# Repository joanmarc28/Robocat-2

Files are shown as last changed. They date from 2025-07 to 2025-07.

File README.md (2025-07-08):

<h1 align="center">
  <br>
    RoboCat Logo
  <br>
    RoboCat
  <br>
</h1>

<h4 align="center">A quadruped robot developed by third-year Computer Science students at the Universitat Autònoma de Barcelona.</h4>

<p align="center">
  <!----------------------- UAB | Robótica ----------------------->
  
  <!--------------------------- Status --------------------------->
  
  <!---------------------------  Raspi --------------------------->
  <a href="https://www.raspberrypi.com/">
  </a>
  <!--------------------------- THX U ---------------------------->
  
  
</p>

 <!---Modificar per els nostres casos--->
<p align="center">
  <a href="#What-is-RoboCat">What is RoboCat?</a> •
  <a href="#How-To-Use">How to use</a> •
  <a href="#Components">Components</a> •
  <a href="#Software">Software</a> •
  <a href="#Tech-Stack">Tech Stack</a> •
  <a href="#License">License</a> •
  <a href="#Contribution">Contribution</a> •
  <a href="#References">References</a> •
  <a href="#Credits">Credits</a> •
  <a href="#Gallery">Gallery</a>
</p>



# What is RoboCat?

RoboCat is an autonomous quadruped robot designed to patrol public streets and monitor parking zones regulated by payment. Its structure and external appearance are inspired by a cat's shape, making it functional but also friendly and approachable for pedestrians.
Equipped with sensors, cameras and onboard computing, RoboCat can detect whether a parked vehicle has an active parking permit, combining robotics, computer vision and real-time data processing to offer a smart, mobile solution for urban mobility enforcement.

The project's main goals are to:
  - Automate parking control in regulated areas
  - Reduce the need for manual inspection
  - Integrate urban robotics with a friendly and non-threatening design
  - Demonstrate the application of robotics in real-world city environments

<p align="center">
  <a href="https://www.youtube.com/watch?v=SMAzvaqW83E" target="_blank">
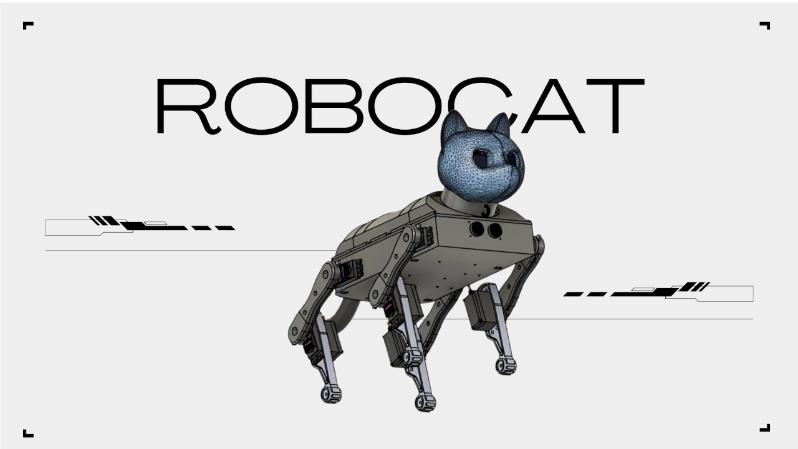
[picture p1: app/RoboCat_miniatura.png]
Miniatura del vídeo
    
  </a>
</p>
<p>
  <a href="https://www.youtube.com/watch?v=SMAzvaqW83E" target="_blank">
    View Video on YouTube
  </a>
</p>
  
# How to use

To set up and run RoboCat on your system, follow these simple steps:
### Step 1: Download the repository
Open your terminal and run the following command:
```bash
git clone https://github.com/joanmarc28/Robocat.git
cd Robocat
```
### Step 2: Install dependencies
Make sure you have Python installed. You can install the required environment simply by running the file setup_robocat.sh:
```bash
bash setup_robocat.sh
```
You can run this command even if the robot is powered off. The setup process only installs software on your computer.

#### How do I install Python?
If you don't have Python installed, download it from the [official website](https://www.python.org/downloads/)
You can check your Python version by running:
```bash
python --version
```
### Step 3: Activate the environment
Once the installation is complete, activate the virtual environment and run the main program by running the following command:
```bash
bash start_robocat.sh
```
Now you can just enjoy!

# Components

## Hardware 

The RoboCat prototype integrates various electronic modules connected to the Raspberry Pi 4, which is the central processing unit.

### Required components
| Component | Model | Units |
|---|---|---|
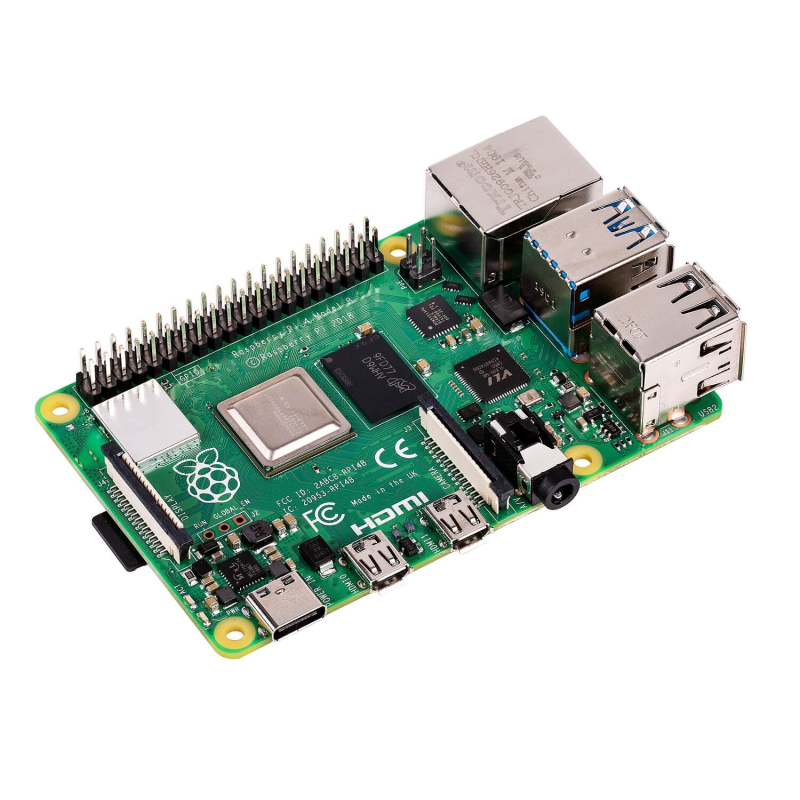
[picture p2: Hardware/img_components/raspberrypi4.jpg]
|  | [Raspberry Pi 4 Model B](https://tienda.bricogeek.com/placas-raspberry-pi/1330-raspberry-pi-4-model-b-4-gb.html) | 1 |
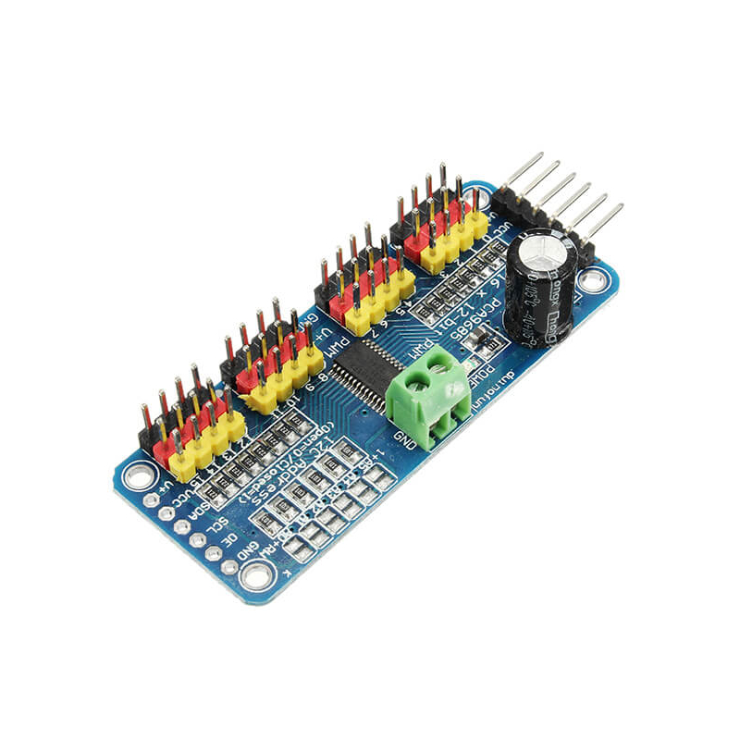
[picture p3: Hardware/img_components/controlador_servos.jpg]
|  | [PCA9685 (16 channel PWM controller)](https://tienda.bricogeek.com/controladores-motores/1764-controlador-pwm-16-canales-i2c-pca9685.html) | 1 |
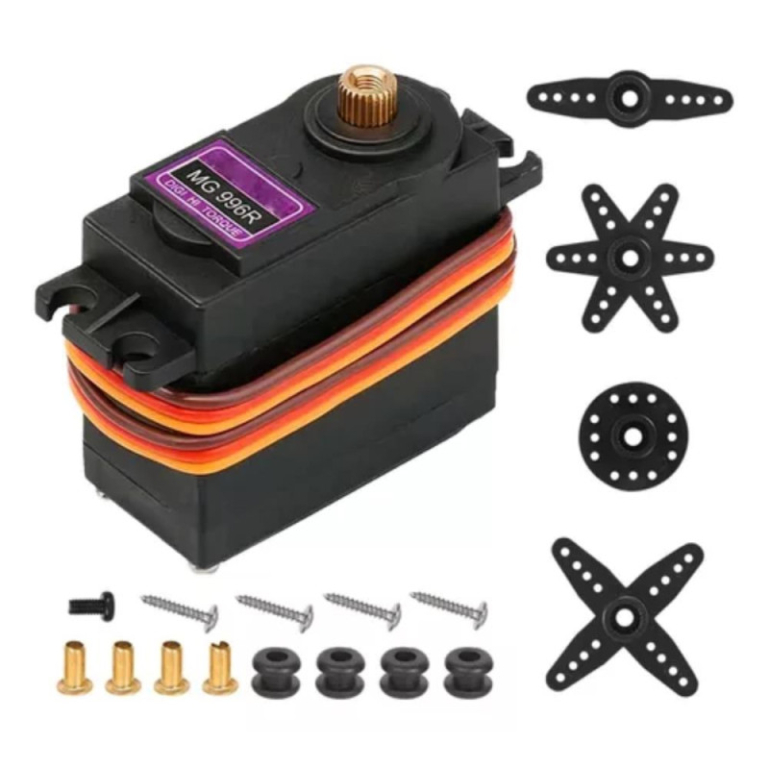
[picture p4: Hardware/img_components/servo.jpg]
|  | [MG996R Digital Servomotor](https://tienda.bricogeek.com/servomotores/1684-servomotor-digital-mg996r.html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) | 9 |
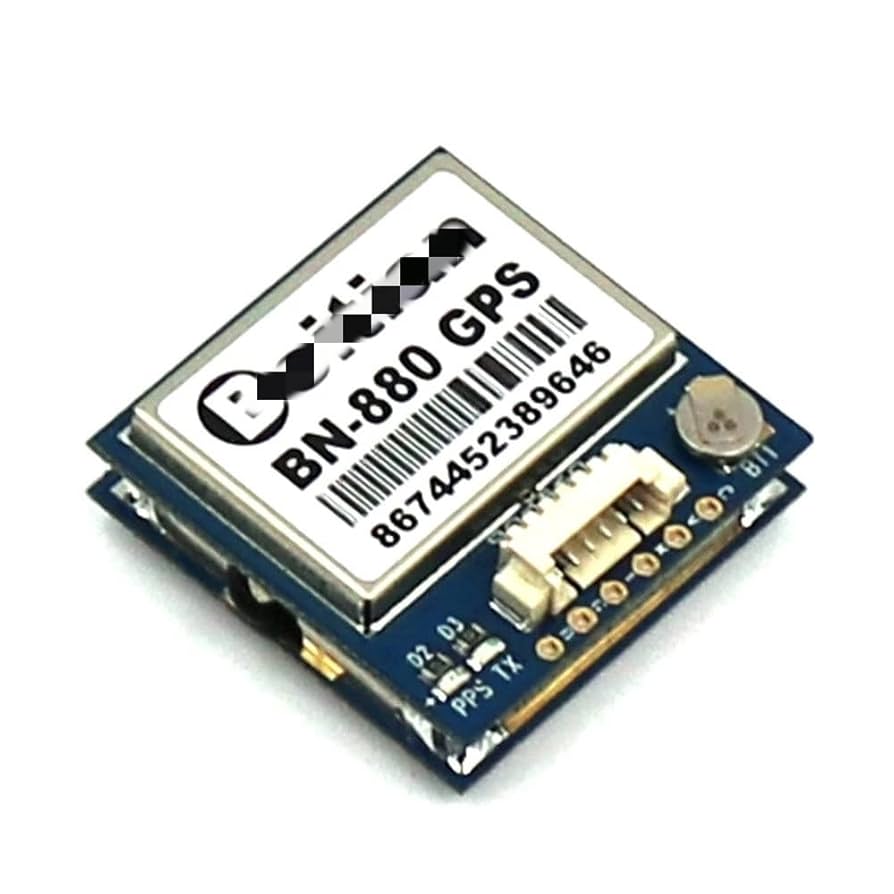
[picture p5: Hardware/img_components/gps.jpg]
|  | [GPS BN-880 (Dual GPS/GLONASS with integrated compass)](https://tienda.bricogeek.com/modulos-gps/1638-gps-glonass-dual-bn-880-con-antena.html) | 1 |
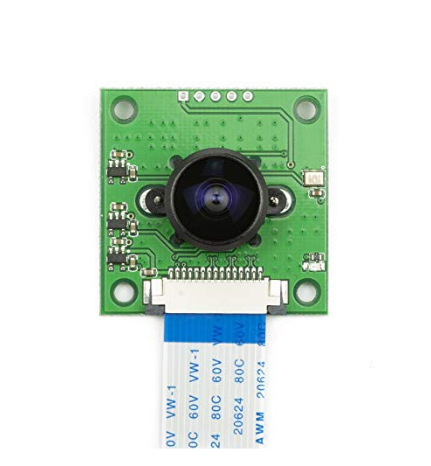
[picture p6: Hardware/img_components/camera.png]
|  | [Camera OV5647 for Raspberry Pi (V2)](https://tienda.bricogeek.com/accesorios-raspberry-pi/822-camara-raspberry-pi-v2-8-megapixels.html) | 1 |
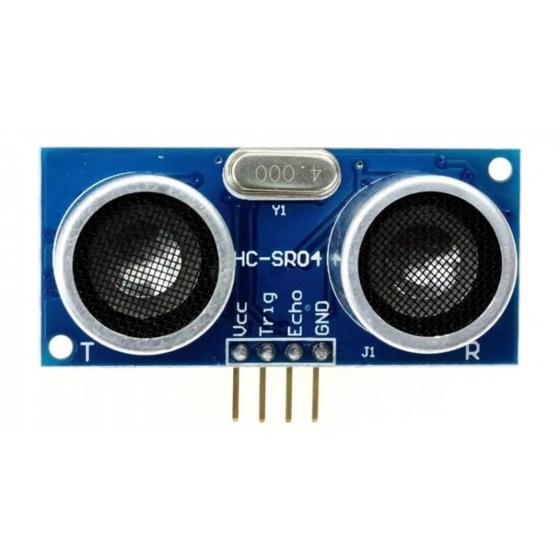
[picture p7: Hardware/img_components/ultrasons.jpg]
|  | [Ultrasonic Distance Sensor HC-SR04](https://tienda.bricogeek.com/sensores-distancia/741-sensor-de-distancia-por-ultrasonidos-hc-sr04.html) | 1 |
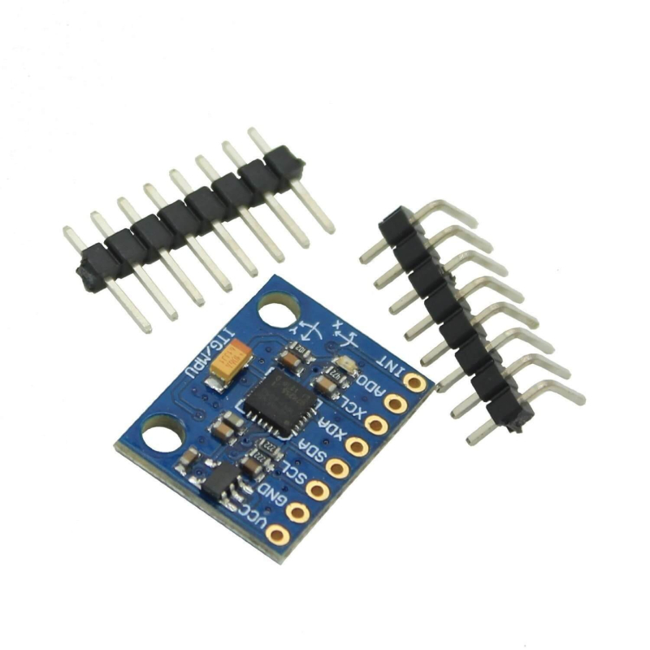
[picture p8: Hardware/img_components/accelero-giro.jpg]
|  | [GY-521 MODULE (MPU-6050 accelerometer and gyro)](https://tienda.bricogeek.com/acelerometros/1682-modulo-gy-521-acelerometro-y-giroscopio-mpu-6050.html) | 1 |
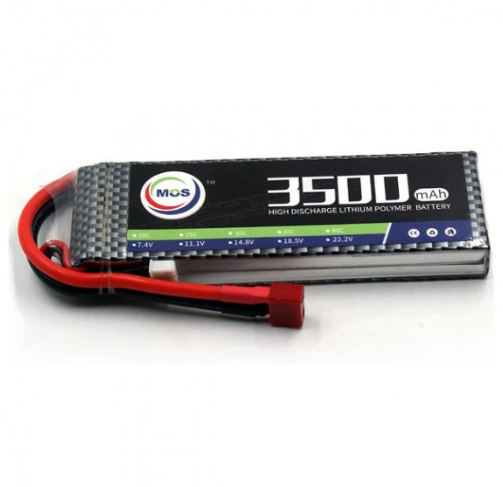
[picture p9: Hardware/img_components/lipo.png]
|  | [3500mAh 2S 25C LiPo Battery (7.4V)](https://tienda.bricogeek.com/baterias-lipo/1156-bateria-lipo-3500mah-2s-25c-74v.html) | 2 |
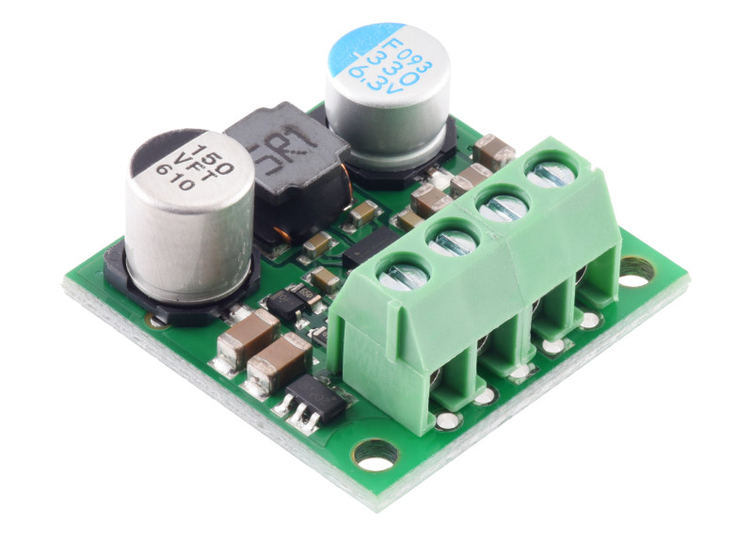
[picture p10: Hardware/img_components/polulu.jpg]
|  | [DC-DC 5V 3A - S13V30F5 Voltage Conversor](https://tienda.bricogeek.com/convertidores-de-voltaje/1746-conversor-dc-5v-3a-s13v30f5.html) | 2 |
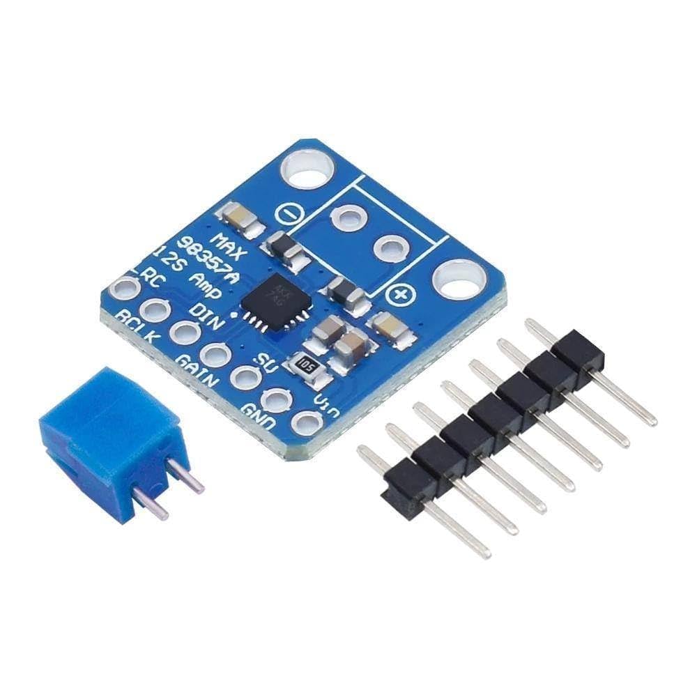
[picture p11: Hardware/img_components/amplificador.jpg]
|  | [FEICHAO 8A UBEC 2-6S LiPo (In 7V-25.5V, Out 12A)](https://www.amazon.es/dp/B07DD9L6P6?ref=ppx_yo2ov_dt_b_fed_asin_title) | 1 |
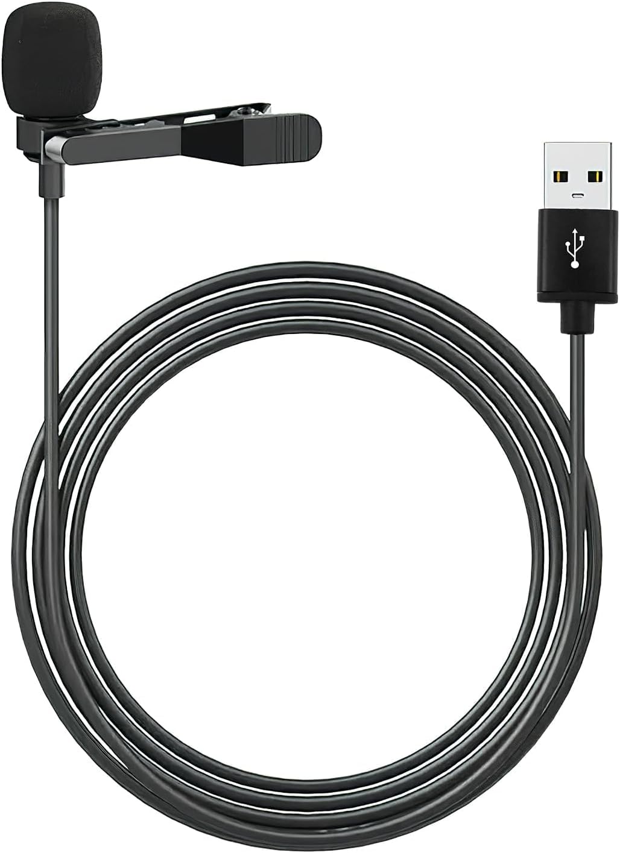
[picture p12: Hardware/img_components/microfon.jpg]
|  | [eModwey Microphone Lavalier USB 2M](https://www.amazon.es/dp/B0DNDT5DRQ?ref=ppx_yo2ov_dt_b_fed_asin_title) | 1 |
|  | [Audio Amplificator I2S MAX98357 (3W)](https://tienda.bricogeek.com/accesorios-raspberry-pi/867-amplificador-de-audio-i2s-max98357a-3w.html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) | 1 |
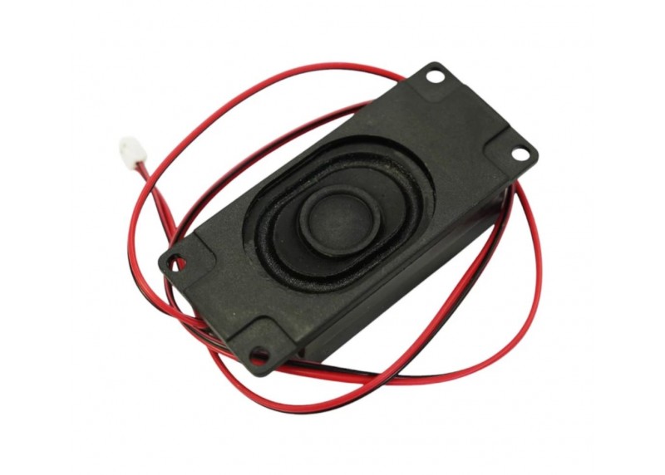
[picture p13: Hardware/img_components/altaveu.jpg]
|  | [Speaker in Box (Ref: PRO-0162)](https://tienda.bricogeek.com/varios/938-altavoz-con-caja-3w.html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) | 1 |
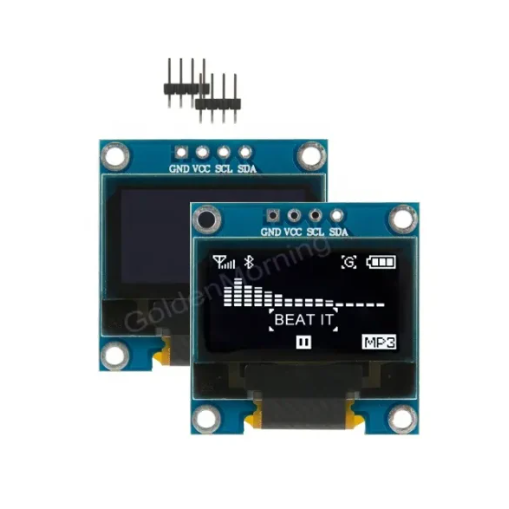
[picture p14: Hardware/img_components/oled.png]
|  | [OLED Screen Module SSD1306 GME12864-11-12-13 (0.96in, 128x64)](https://goldenmorninglcd.com/es/m%C3%B3dulo-de-pantalla-oled/0.96-pulgadas-128x64-ssd1306-gme12864-11/) | 2 |
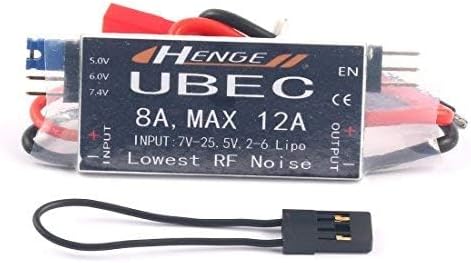
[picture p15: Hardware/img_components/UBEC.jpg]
|  | [FEICHAO 8A UBEC Salida MAX 12A Entrada 7V-25.5V 2-6S Lipo](https://www.amazon.es/dp/B07DD9L6P6?ref=ppx_yo2ov_dt_b_fed_asin_title) | 1 |

### Wiring Schematics
The wiring schematics shown below have been created using Fritzing for clarity during the assembly process.
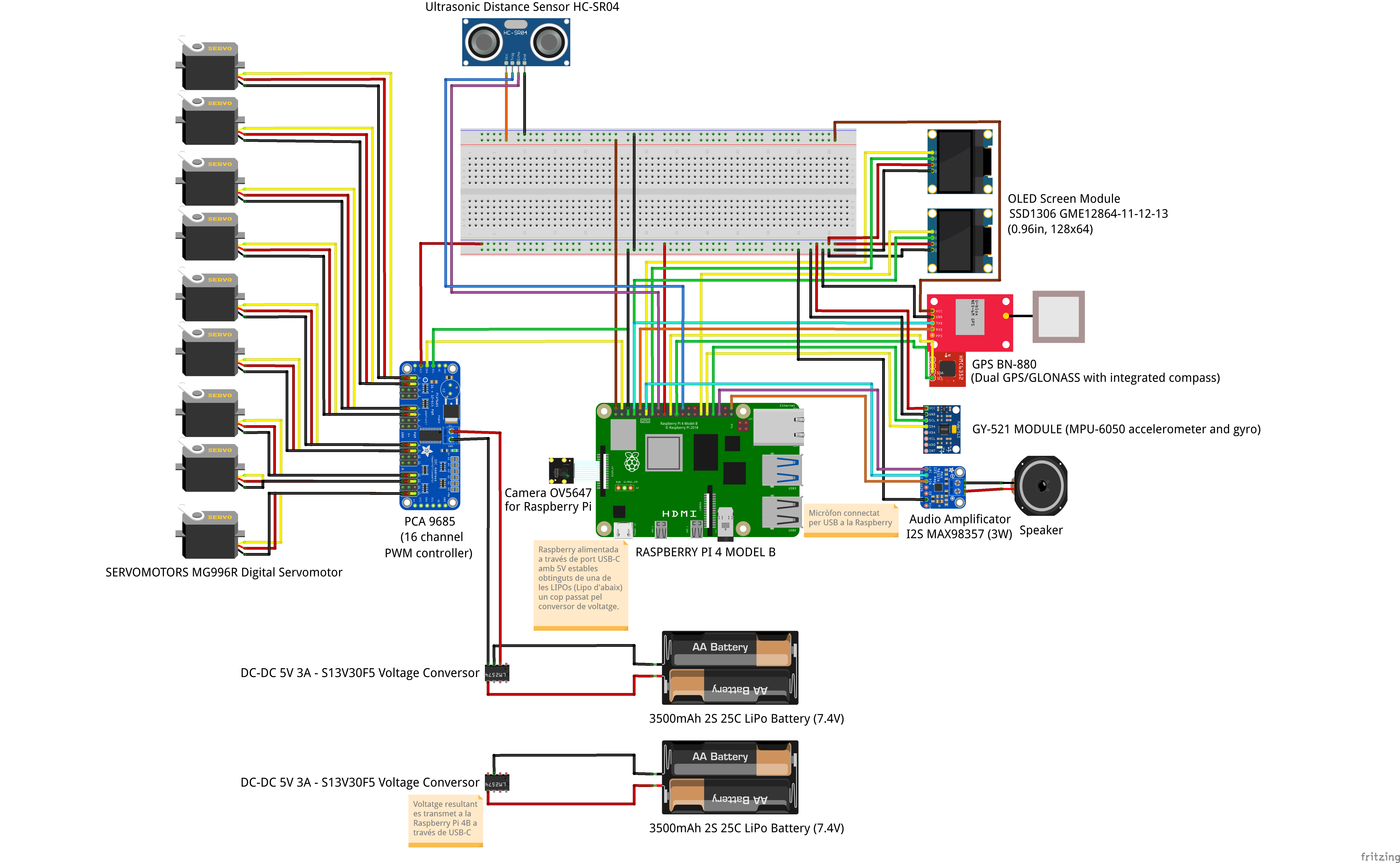
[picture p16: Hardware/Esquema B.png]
 <br>

> [!NOTE]
> However, a custom PCB has been designed using EasyEDA to ensure a compact assembly for the final RoboCat unit, which can be seen in the following <a href="https://github.com/joanmarc28/Robocat/blob/main/Hardware/PCB%20Robocat%20Disseny.png">link.</a>

## 3D Design

All RoboCat 3D parts have been designed using Autodesk Fusion 360. The structure is divided into the following parts, and the printing parameters for each piece can be found in its corresponding folder.

### Legs
| Full Leg |
|----------|
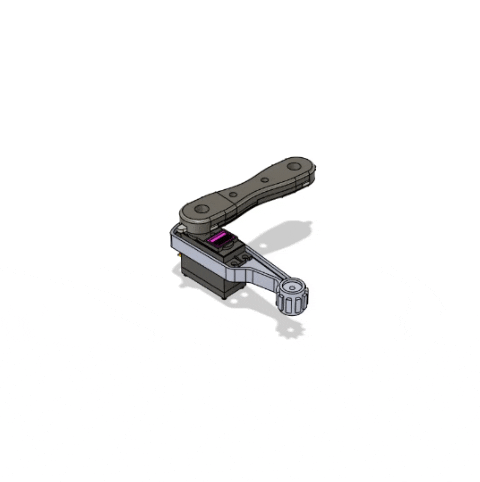
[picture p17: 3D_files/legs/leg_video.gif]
| <div align="center"> <br>[Leg (View Files)](https://github.com/joanmarc28/Robocat/blob/main/3D_files/legs)</div> |

---

### Body

| Chassis | Second Floor Plate |
|---|---|
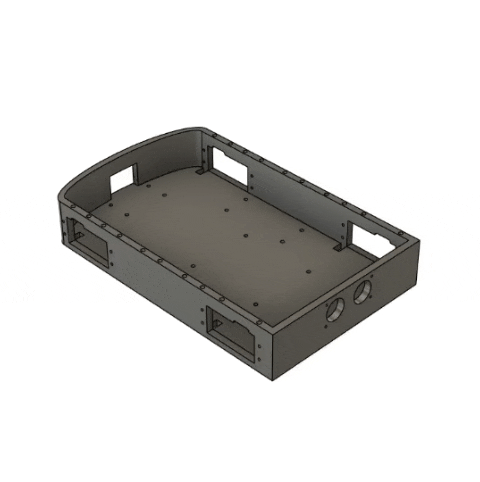
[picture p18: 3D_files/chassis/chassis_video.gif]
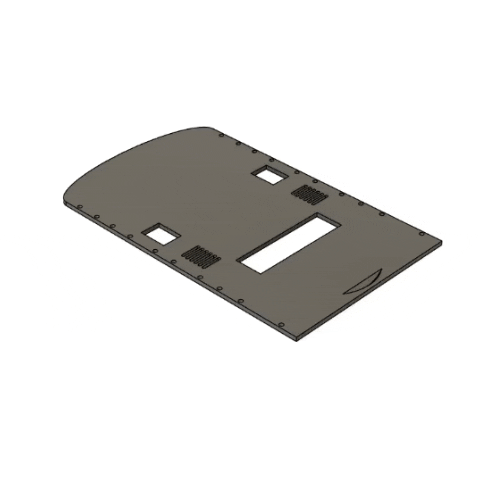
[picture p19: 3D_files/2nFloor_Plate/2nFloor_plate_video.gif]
| <div align="center">  <br> [Chassis (View File)](https://github.com/joanmarc28/Robocat/blob/main/3D_files/chassis) </div> | <div align="center">   <br> [2nd Floor Plate (View File)](https://github.com/joanmarc28/Robocat/blob/main/3D_files/2nFloor_Plate) </div>|

| Front Body | Middle Body | Back Body |
|---|---|---|
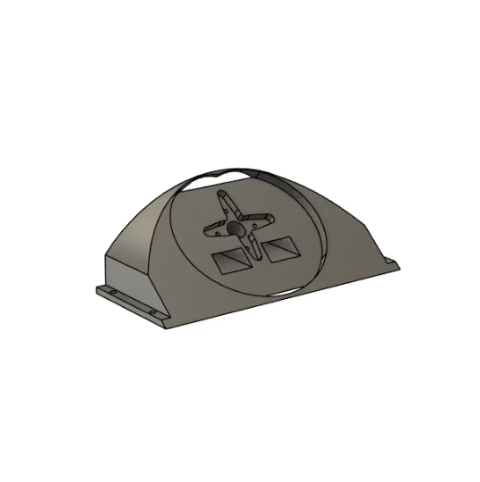
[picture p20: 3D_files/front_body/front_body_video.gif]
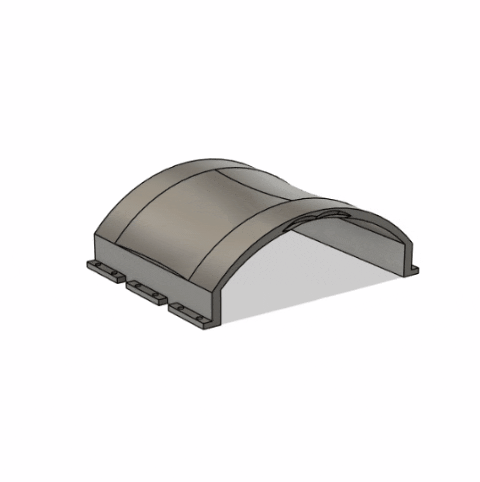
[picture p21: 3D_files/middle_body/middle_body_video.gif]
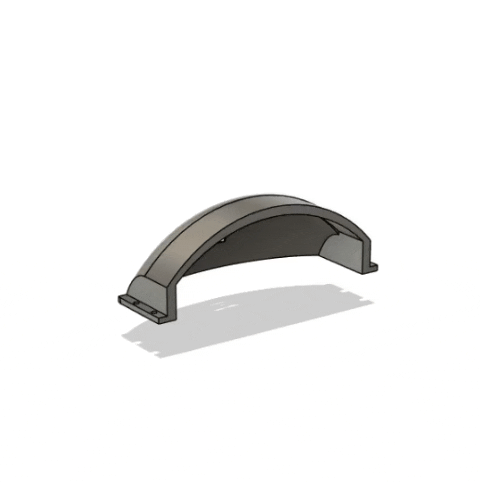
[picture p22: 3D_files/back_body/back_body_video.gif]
| <div align ="center">  <br> [Front Body (View File)](https://github.com/joanmarc28/Robocat/blob/main/3D_files/front_body) </div> | <div align="center">  <br> [Middle Body (View File)](https://github.com/joanmarc28/Robocat/blob/main/3D_files/middle_body) </div> | <div align="center">  <br> [Back Body (View File)](https://github.com/joanmarc28/Robocat/blob/main/3D_files/back_body) </div> |

---

### Head

| Neck | Head Model | Head Back Panel |
|---|---|---|
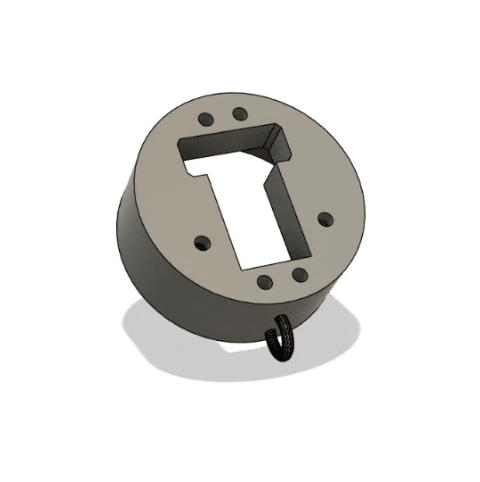
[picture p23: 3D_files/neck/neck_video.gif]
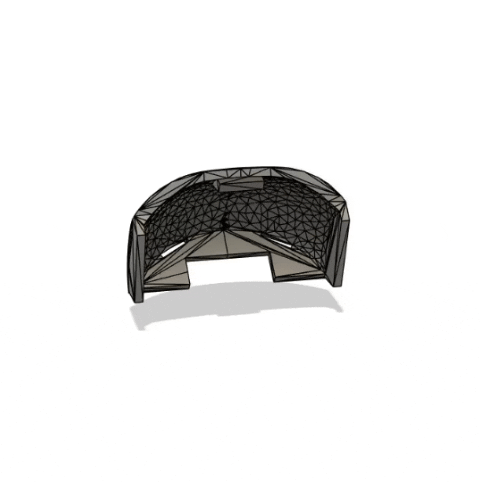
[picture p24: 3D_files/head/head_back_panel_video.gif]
| <div align = "center">  <br>  [Neck (View File)](https://github.com/joanmarc28/Robocat/blob/main/3D_files/neck) </div> | <div align="center">  <br> [Head Model (View Files)](https://github.com/joanmarc28/Robocat/blob/main/3D_files/head) </div> | <div align="center">   <br> [Head Back Panel (View Files)](https://github.com/joanmarc28/Robocat/blob/main/3D_files/head) </div> |

---

### Miscellaneous

| Tail | Fan |
|---|-----|
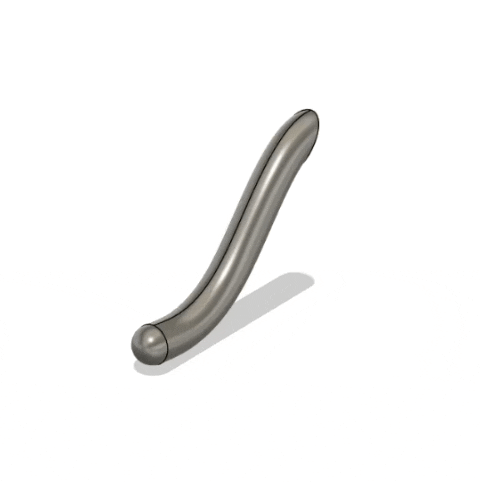
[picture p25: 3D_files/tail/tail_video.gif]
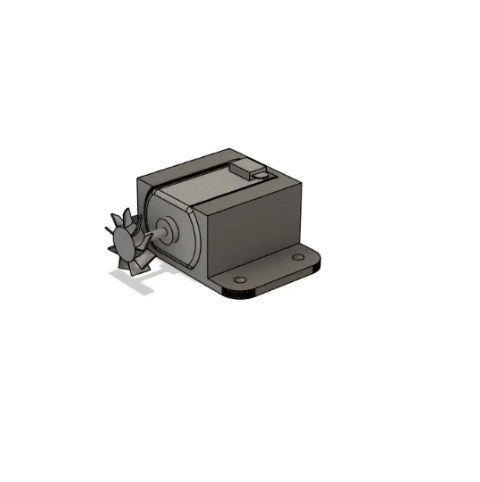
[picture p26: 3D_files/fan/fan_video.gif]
| <div align = "center">  <br> [Tail (View File)](https://github.com/joanmarc28/Robocat/blob/main/3D_files/tail/tail.stl) </div> | <div align="center">   <br> [Fan (View Files)](https://github.com/joanmarc28/Robocat/blob/main/3D_files/fan)</div> |

---

# Software
The RoboCat software is composed of three main components:
- License Plate Detection Algorithm
- Inverse Kinematics for Walking
- Web Application

## License Plate Detection Algorithm
RoboCat integrates a computer vision system that operates in three phases to detect and process license plates:
#### 1. Vehicle Detection
Using YOLOv8n object detection model, RoboCat identifies vehicles present in its field of vision. Specifically, the system is trained to detect only conventional passenger cars, the only object class configured in the YOLO model for this detection task. This selective approach ensures optimized performance and reduces false positives from unrelated objects.

<p align="center">
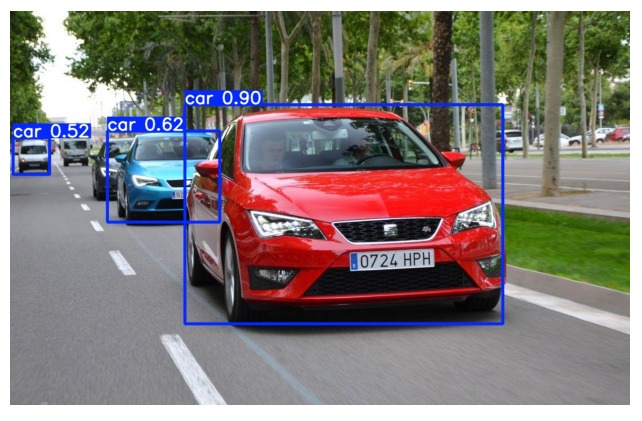
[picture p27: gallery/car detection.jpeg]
Car detection
    
</p>

#### 2. License Plate Detection
Once a vehicle is detected, a second YOLOv8n model is used to locate the license plate area accurately. The system also detects and extracts the nationality region by identifying the blue section commonly present on Spanish license plates. Since our project only focuses on Spanish license plates, the blue section is cropped for further processing.

<p align="center">
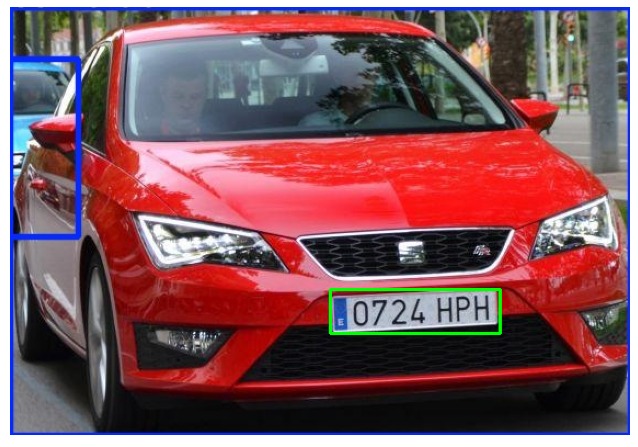
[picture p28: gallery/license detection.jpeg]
plate detection
  &nbsp;&nbsp;&nbsp;&nbsp;cutted plate
</p>

#### 3. Optical Character Recognition (OCR)
For text extraction from license plates, RoboCat uses Gemini AI, a multimodal system capable of performing OCR tasks with high accuracy, eliminating the need for manual character segmentation and traditional CNN-based recognition.
However, the project includes a complete implementation of an OCR system based on a TensorFlow Convolutional Neural Network (CNN), which can serve as a backup or for research purposes. This CNN model performs character segmentation, individual recognition, and post-processing to ensure compliance with the Spanish license plate format (e.g., 1234 BCD), including correction mechanisms to mitigate common character misclassification.

<p align="center">
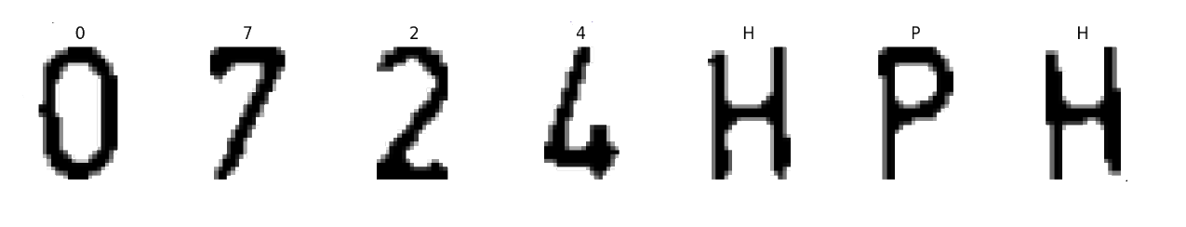
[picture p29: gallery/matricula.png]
Character identification
    
</p>

## Inverse Kinematics for Walking
<table style="border: none;" >
<tr>
<td width="40%">
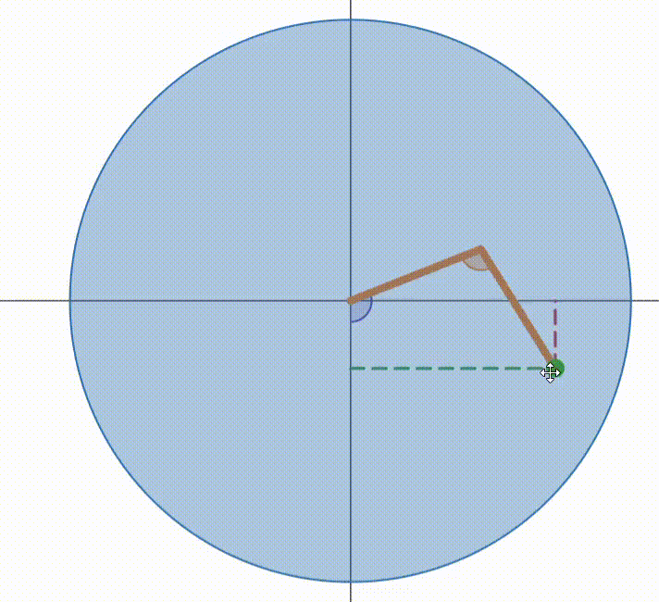
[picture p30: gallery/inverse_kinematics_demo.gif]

</td>
<td>

RoboCat's locomotion is based on an Inverse Kinematics system, which allows precise control of the robot's legs to perform complex movements such as walking or interacting with its environment. Unlike forward kinematics, where joint angles are known and the resulting position is computed, inverse kinematics solves the opposite problem: determining the necessary joint angles to achieve a desired position or orientation of the legs.

The inverse kinematics models and animations have been designed and tested using CoppeliaSim, a robotics simulation environment, allowing us to prototype and optimize the movements before deployment on the real robot.

Currently, RoboCat supports the following pre-programmed movement modes using inverse kinematics.

</td>
</tr>
</table>

 | Walk | Sit | Playful |
 |------|-----|---------|
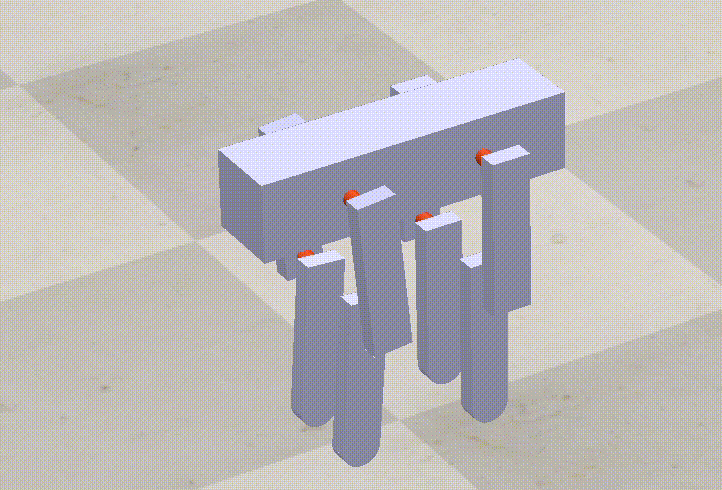
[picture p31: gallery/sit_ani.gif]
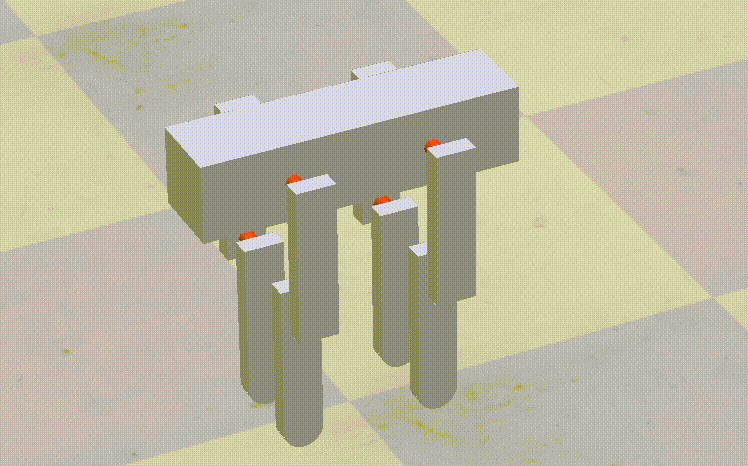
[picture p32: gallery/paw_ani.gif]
 |  |  |  |

## Web Application
The RoboCat system is built on a layered software architecture that separates concerns across user interaction, server-side processing, and robot-level execution. This structured approach enhances modularity, scalability, and maintainability while enabling seamless coordination between autonomous robotic units and central control. The following diagram illustrates the core components and responsibilities distributed across the User, Server, and Robot levels.

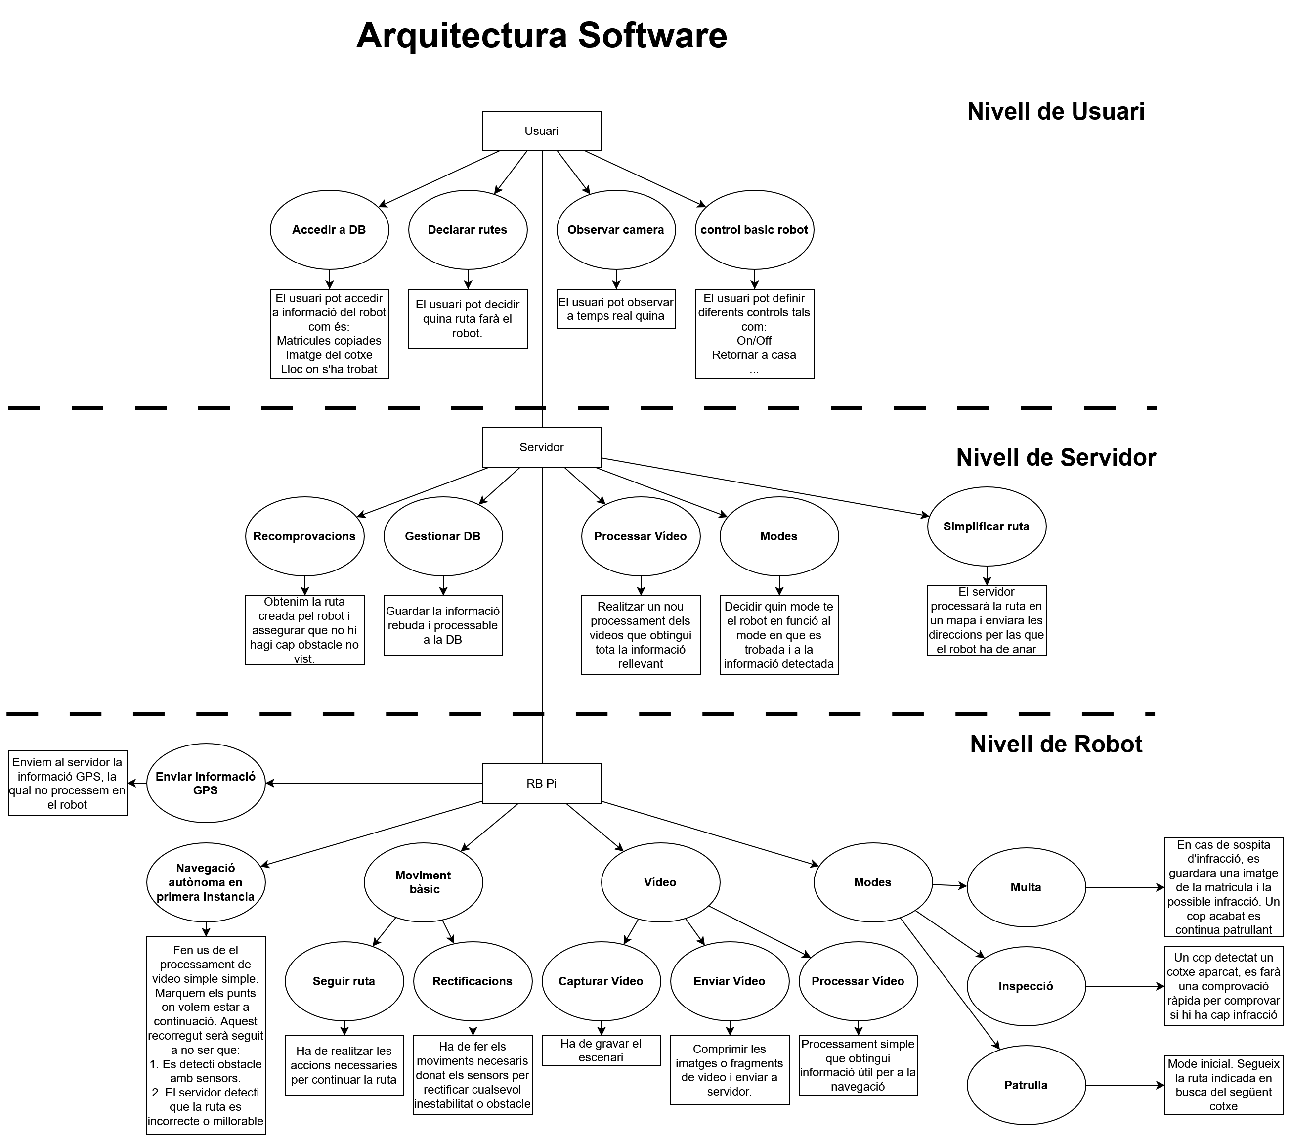
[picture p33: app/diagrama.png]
<br>
As we can see, the web application includes two user profiles.

### Police Officer
Authorized officers can access a control interface to monitor and manage RoboCat units in real-time:
- Live location tracking (GPS coordinates)
- Internal system monitoring, including controller temperature
- Real-time video feed from RoboCat's onboard camera
- Remote control commands such as "Crouch" or "Stand Up"

In addition, officers can manage regulated parking areas through the Parking Zone Management page, where new parking zones can be defined by specifying latitude and longitude boundaries.
Officers also have access to the Infraction Database, where they can review all detected violations, manually validate or dismiss possible infractions, and issue fines when necessary.
<p>
  <a href="https://www.youtube.com/watch?v=kHLnomrDODU" target="_blank">
    Miniatura del vídeo
  </a>
</p>
<p>
  <a href="https://www.youtube.com/watch?v=kHLnomrDODU" target="_blank">
    View Video on YouTube
  </a>
</p>

### Client (Vehicle Owner)

Registered users can manage their vehicles and parking sessions through the web platform:
- Register one or more vehicles by providing license plate, brand, model and official DGT data.
- Pay for parking in regulated zones by selecting a registered vehicle and specifying the desired parking duration
- Active parking sessions are displayed on the main dashboard with a countdown timer showing the remaining time.

If a vehicle is parked without a valid registration in a regulated area and RoboCat scans its license plate, an infraction is automatically recorded. The system notifies the vehicle owner of the violation and provides the fine details.

<p>
  <a href="https://www.youtube.com/watch?v=OOTuV0h7_Dc" target="_blank">
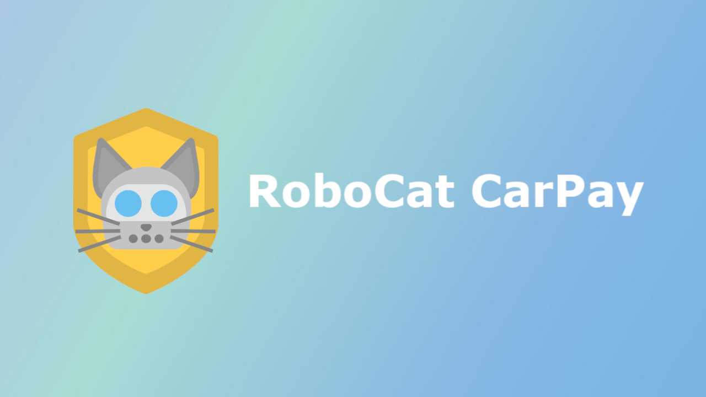
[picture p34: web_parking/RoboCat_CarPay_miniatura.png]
Miniatura del vídeo
    
  </a>
</p>
<p>
  <a href="https://www.youtube.com/watch?v=OOTuV0h7_Dc" target="_blank">
    View Video on YouTube
  </a>
</p>

# Tech Stack
### Programming & AI





  
### 3D Design & Hardware




### Simulation & Development Tools




### Web Application
| Backend | Frontend |
|---|---|
|  |  |

| Database | APIs & External Services |
|---|---|
|  |   <br>   |
  
# License
This project is licensed under the [MIT License](LICENSE).  
© 2025–present [Contributors](https://github.com/joanmarc28/Robocat/contributors)

# Contribution
This project was created as part of a university assignment and is not open to external contributions.

However, feel free to fork the repository and experiment with it for learning and improvement purposes.

# References
**1** | *Tutorial EasyEDA* ([Link](https://www.youtube.com/watch?v=BvvHJ-H79l8&ab_channel=ELECTRONOOBSenEspa%C3%B1ol)) <br>

**2** | *The LAD Dog V1.0 - Assembly Instructions* ([Link](https://www.youtube.com/watch?v=YNgyFZvyQP4&ab_channel=LADRobotics)) <br>

**3** | *OpenCat by PetoiCamp* ([Link](https://github.com/PetoiCamp/OpenCat)) <br>

**4** | *Boston Dynamics Robot* ([Link](https://www.youtube.com/watch?v=9KdLYhsh0zw&ab_channel=SabinIngenier%C3%ADaCivil)) <br>

**5** | *Beitian BN220 GPS Installation* ([Link](https://www.youtube.com/watch?v=30FU0_7-G3w&ab_channel=Unboxingexperience7)) <br>

**6** | *Sistema de detección de matrículas con OpenCV (Jorge Navacerrada)* ([Link](https://oa.upm.es/51869/1/TFG_JORGE_NAVACERRADA.pdf)) <br>

**7** | *Car License Plate Detection Database* ([Link](https://www.kaggle.com/datasets/andrewmvd/car-plate-detection/data)) <br>

**8** | *Chars74K Database for OCR Training* ([Link](https://www.kaggle.com/datasets/supreethrao/chars74kdigitalenglishfont))

# Credits

<table align="center">
  <tr>
    <td align="center" style="border:none;">
      Martí Armengod Villar<br/>
      <span style="font-size:14px;"><strong>Martí Armengod Villar</strong></span><br/>
      <span style="font-size:12px;"><em>SW Lead</em></span>
    </td>
    <td align="center" style="border:none;">
      Lara Castillejo Roig<br/>
      <span style="font-size:14px;"><strong>Lara Castillejo Roig</strong></span><br/>
      <span style="font-size:12px;"><em>Testing & Validation Lead</em></span>
    </td>
    <td align="center" style="border:none;">
      Julia Lipin Gener Rey<br/>
      <span style="font-size:14px;"><strong>Julia Lipin Gener Rey</strong></span><br/>
      <span style="font-size:12px;"><em>3D & Mechanical Lead</em></span>
    </td>
    <td align="center" style="border:none;">
      Joan Marc Samó Rojas<br/>
      <span style="font-size:14px;"><strong>Joan Marc Samó Rojas</strong></span><br/>
      <span style="font-size:12px;"><em>Product Owner</em></span>
    </td>
    <td align="center" style="border:none;">
      Luís Vera Albarca<br/>
      <span style="font-size:14px;"><strong>Luís Vera Albarca</strong></span><br/>
      <span style="font-size:12px;"><em>HW Lead</em></span>
    </td>
  </tr>
</table>

Special thanks to:
- **Pau Bofill** for collaborating with the license plate detection algorithm and making it possible.
- **Marc Bardeli** for collaborating with the web application implementation.

# Gallery
<p align>
RoboCat Logo 
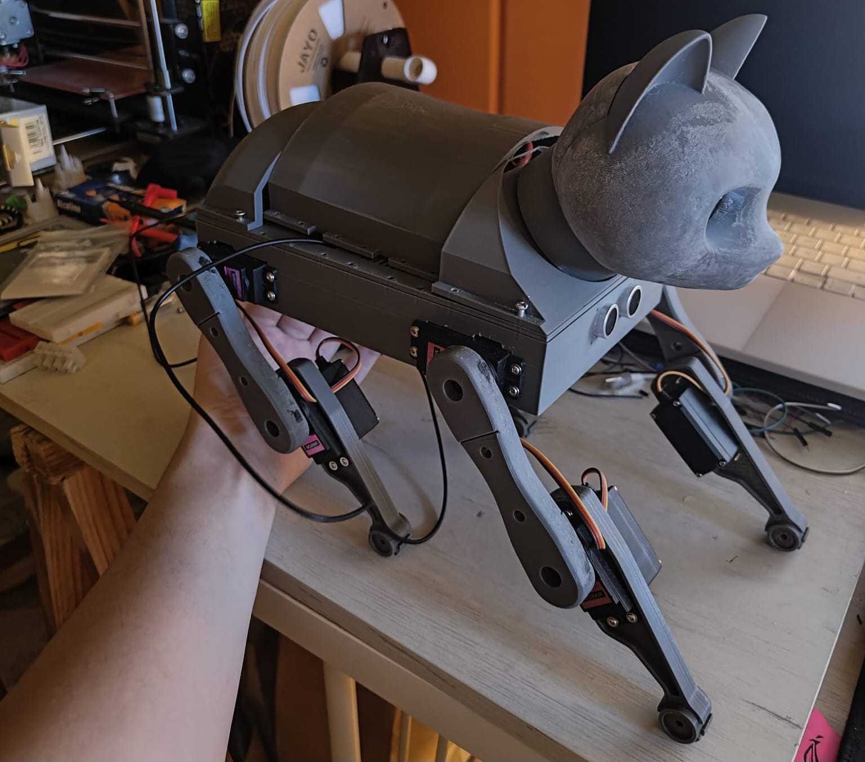
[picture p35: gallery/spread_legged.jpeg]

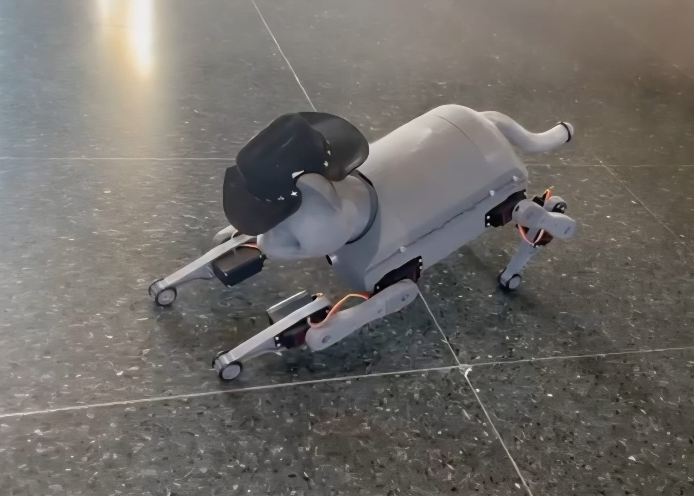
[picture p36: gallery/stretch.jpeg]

RoboCat Logo
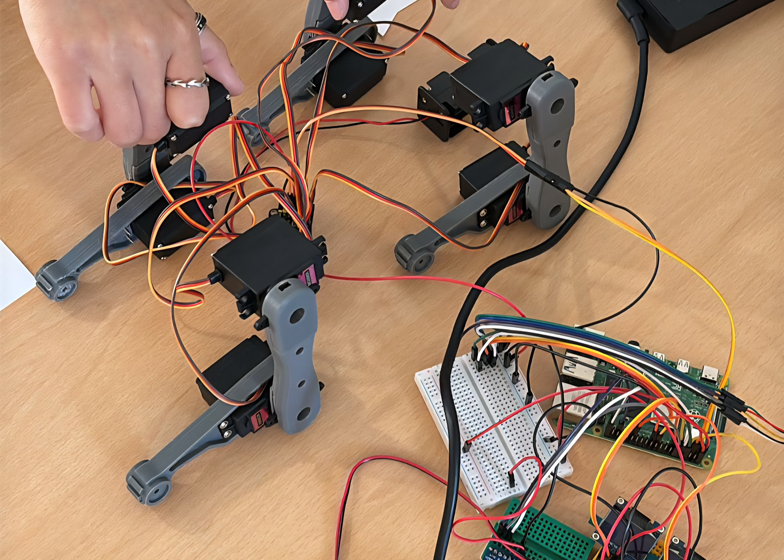
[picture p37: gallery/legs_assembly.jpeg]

RoboCat Logo
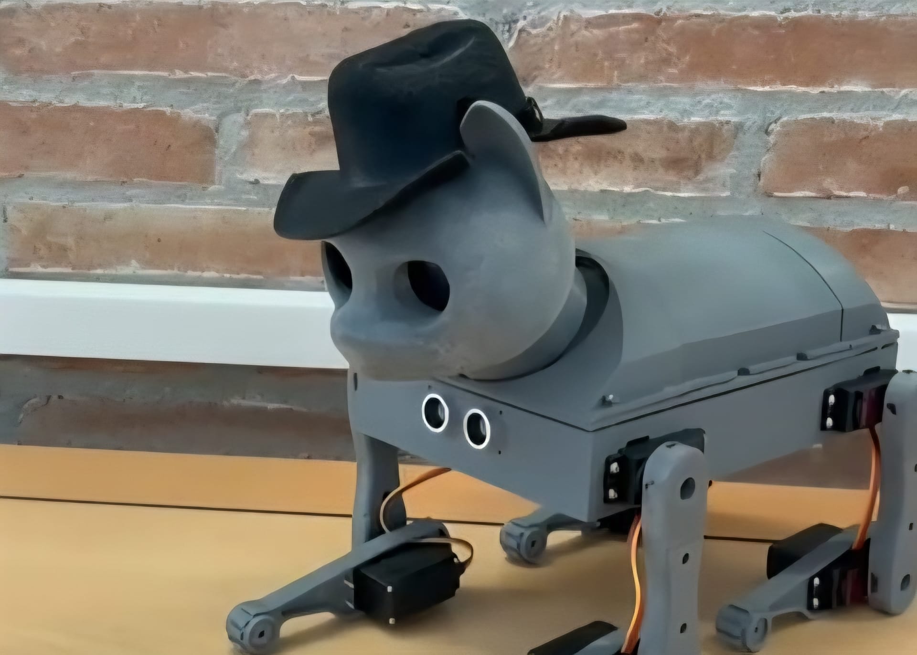
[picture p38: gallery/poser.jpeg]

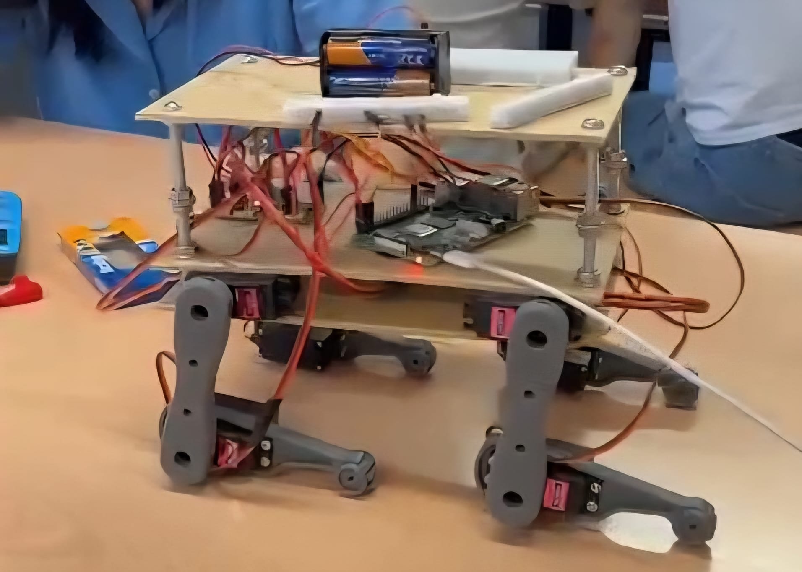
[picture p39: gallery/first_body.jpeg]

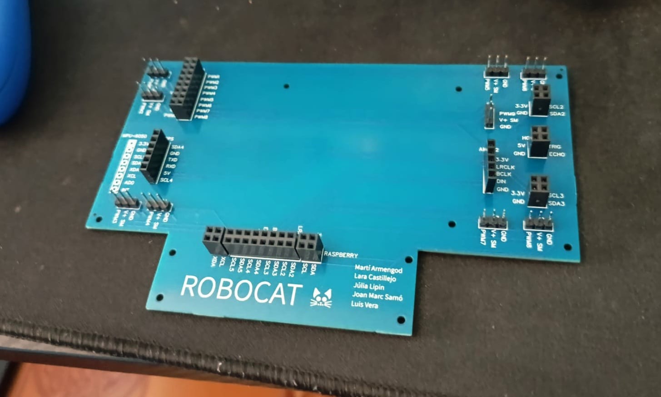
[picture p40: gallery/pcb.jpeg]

RoboCat Logo
</p>

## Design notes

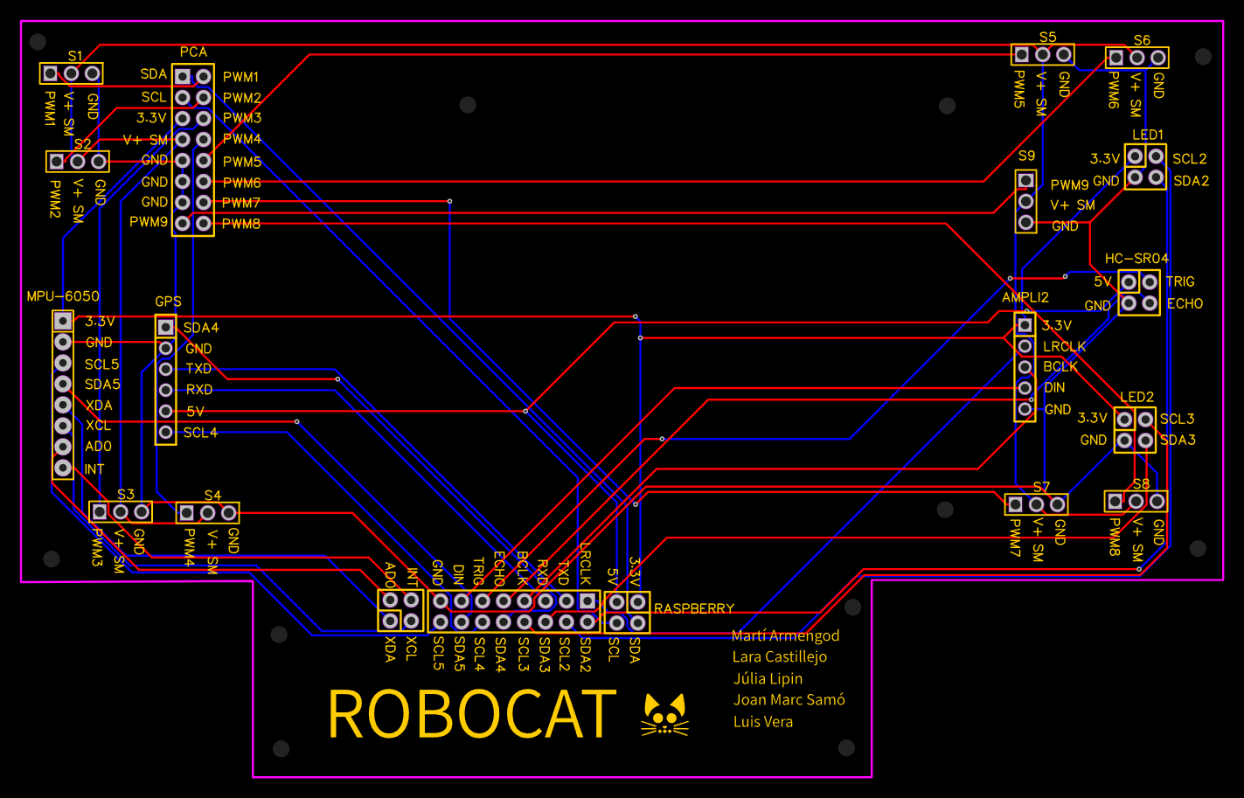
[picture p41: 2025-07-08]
Hardware/PCB Robocat Disseny.png

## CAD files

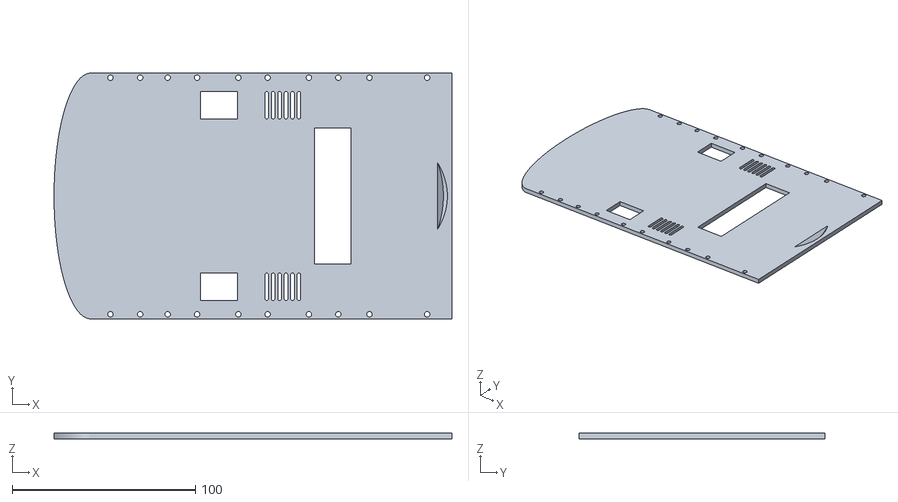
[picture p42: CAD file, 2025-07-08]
3D_files/2nFloor_Plate/2nFloor_Plate.stl
217.0 x 134.0 x 3.00

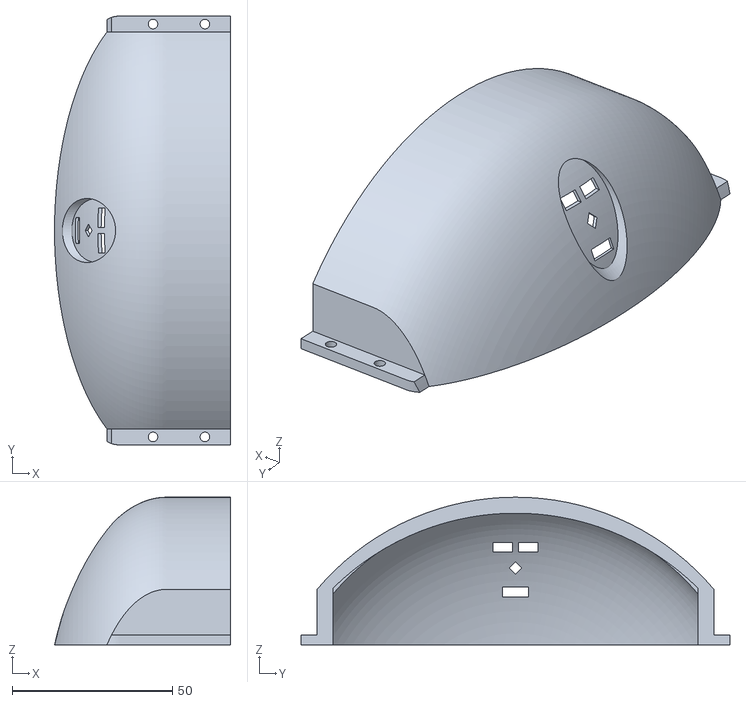
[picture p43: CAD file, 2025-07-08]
3D_files/back_body/back_body.stl
55.0 x 134.0 x 46.1

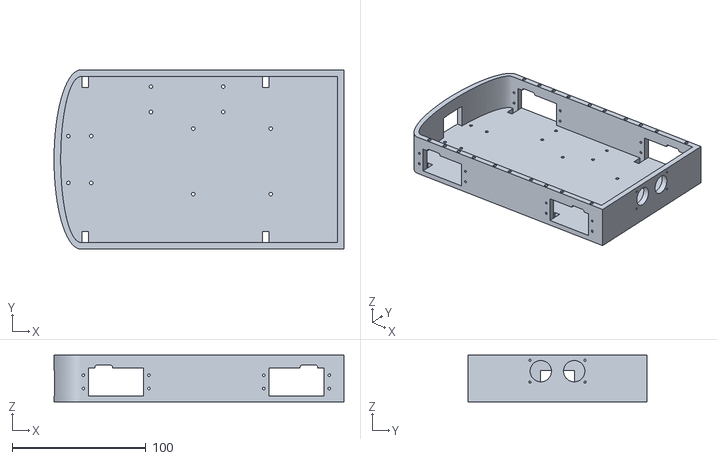
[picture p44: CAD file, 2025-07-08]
3D_files/chassis/chassis.stl
217.0 x 134.0 x 35.0

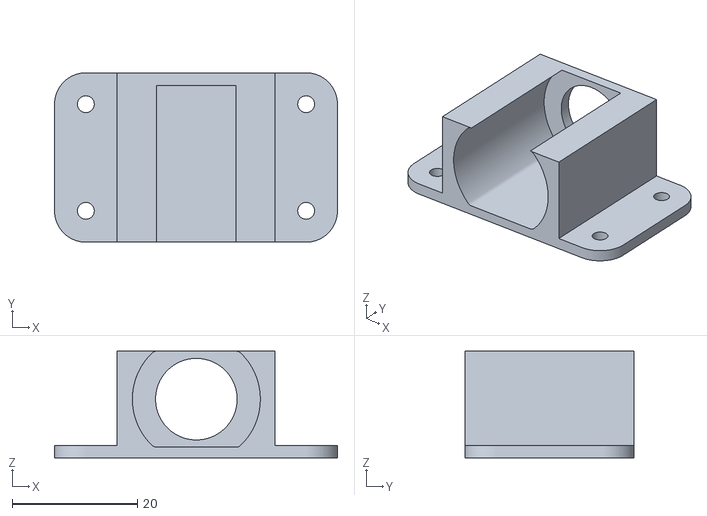
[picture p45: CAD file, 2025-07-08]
3D_files/fan/fan_holder.stl
45.1 x 27.0 x 17.0

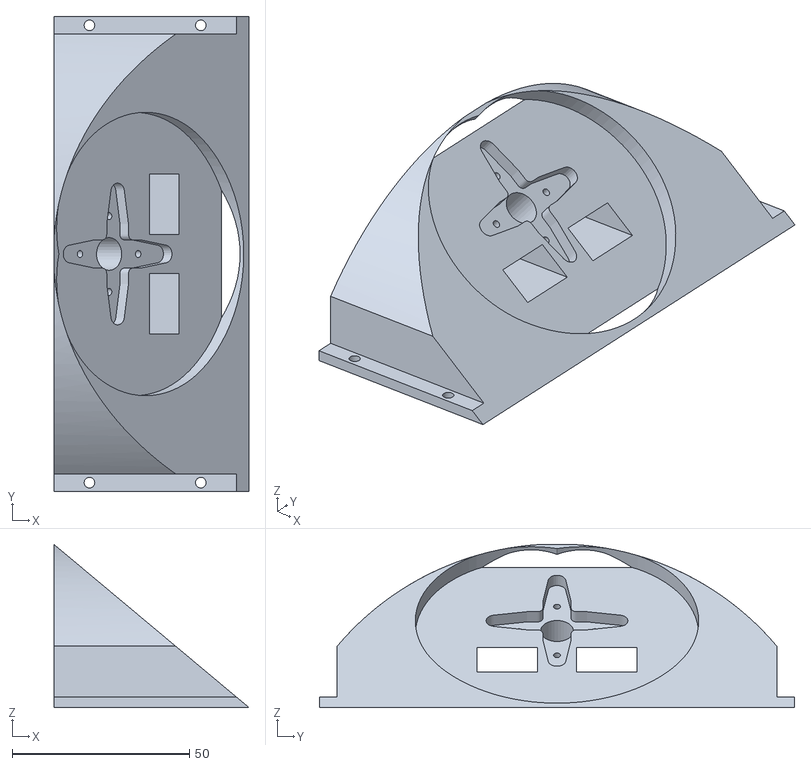
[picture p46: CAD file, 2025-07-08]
3D_files/front_body/front_body.stl
55.0 x 134.0 x 46.0

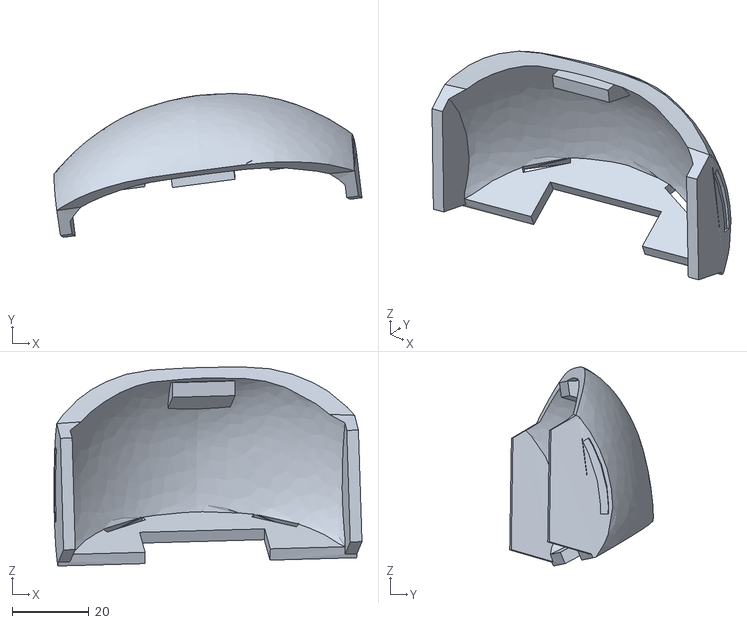
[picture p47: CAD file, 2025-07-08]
3D_files/head/head_back_panel.stl
80.5 x 37.5 x 52.0

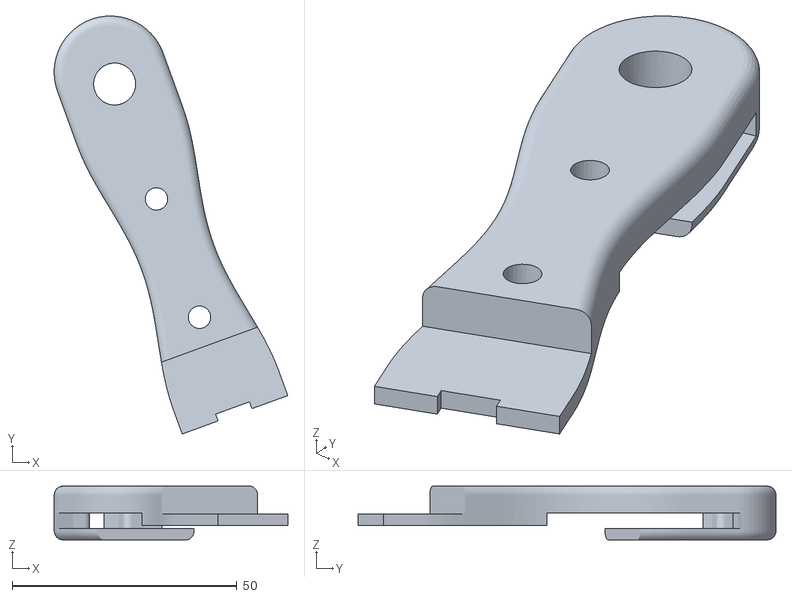
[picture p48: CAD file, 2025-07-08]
3D_files/legs/upper_legFront.stl
52.0 x 93.0 x 12.0

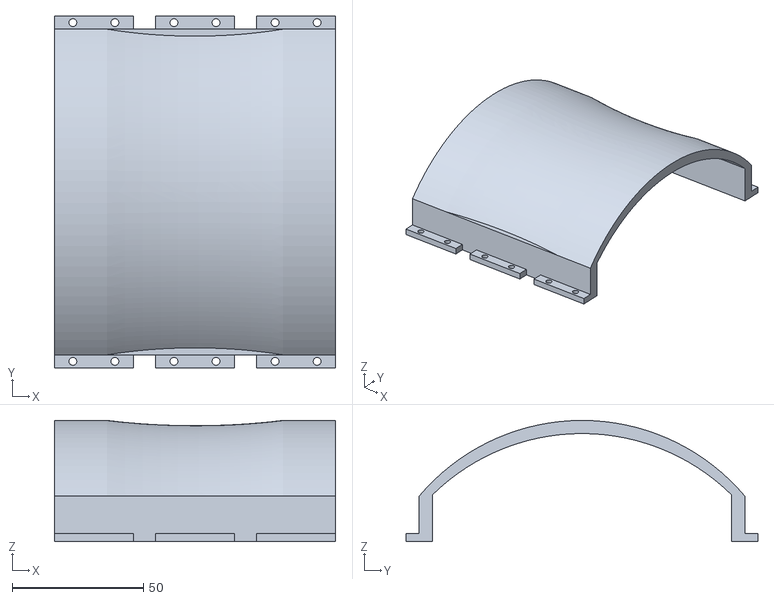
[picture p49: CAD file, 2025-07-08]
3D_files/middle_body/middle_body.stl
107.0 x 134.0 x 46.1

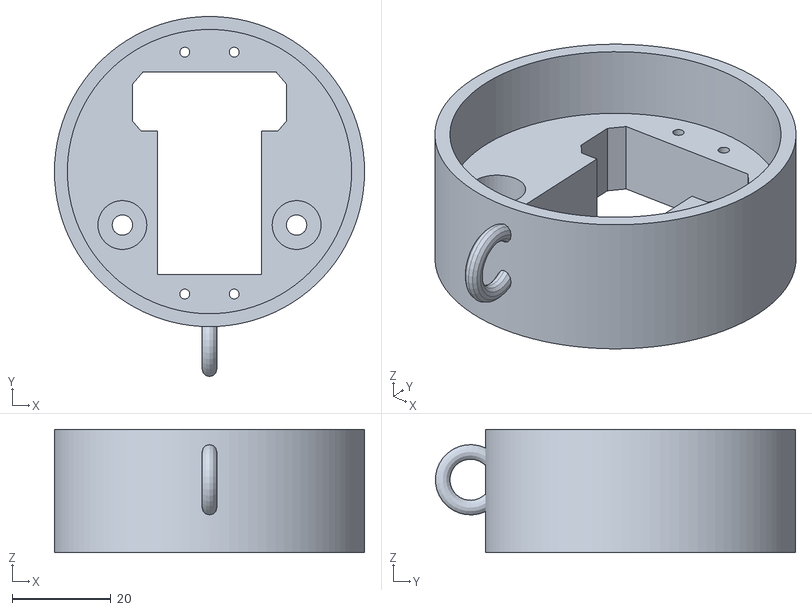
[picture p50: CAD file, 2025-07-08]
3D_files/neck/neck.stl
62.8 x 72.9 x 24.9

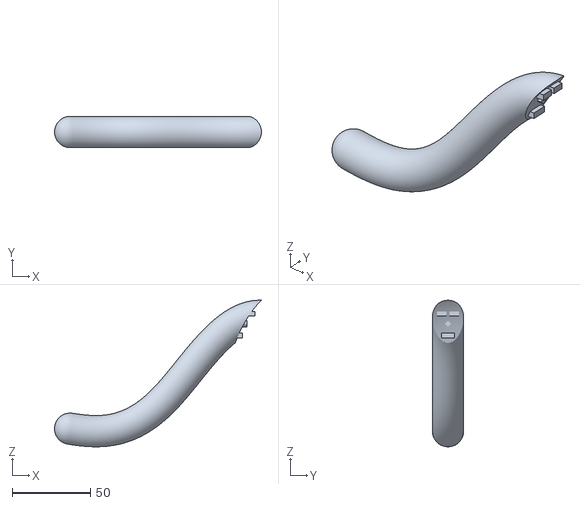
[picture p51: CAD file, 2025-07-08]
3D_files/tail/tail.stl
132.2 x 20.0 x 93.6

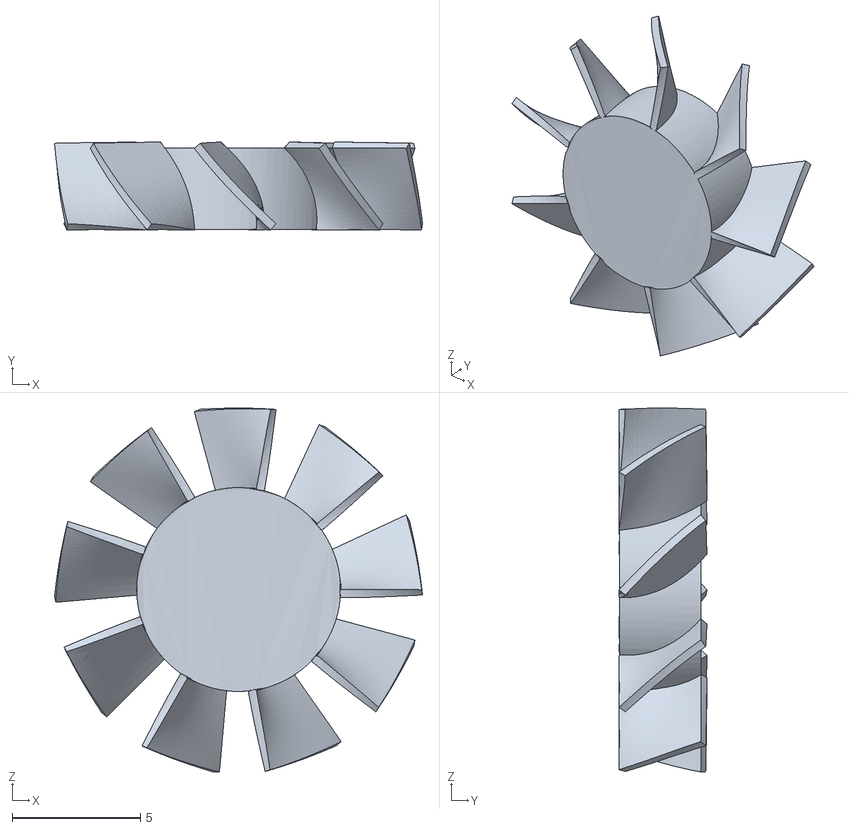
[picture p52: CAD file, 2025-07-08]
3D_files/fan/fan_blades.stl
14.4 x 3.44 x 14.2

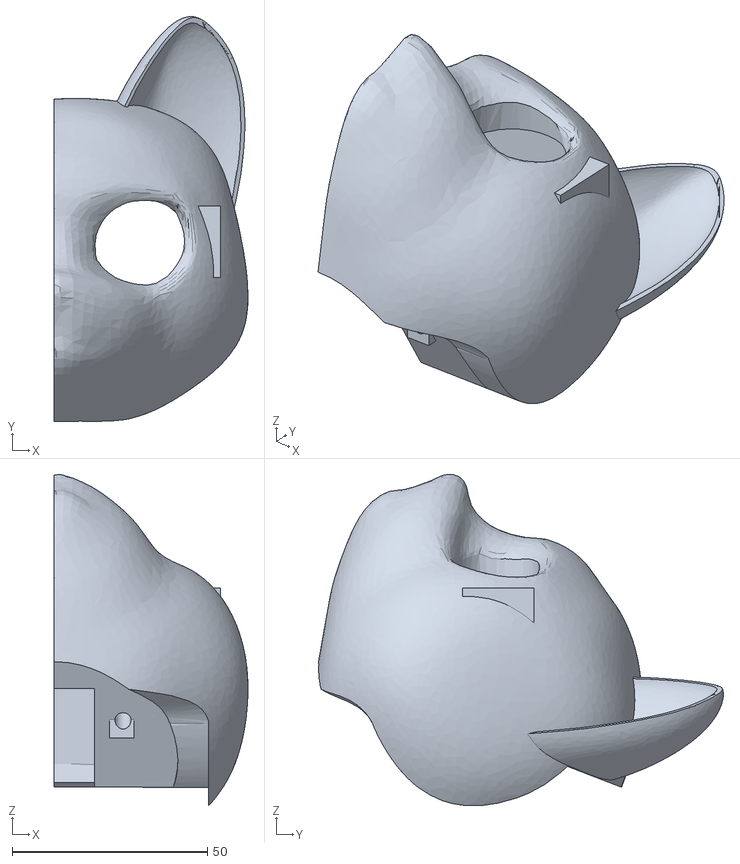
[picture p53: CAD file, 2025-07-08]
3D_files/head/head.stl
49.6 x 103.7 x 84.8

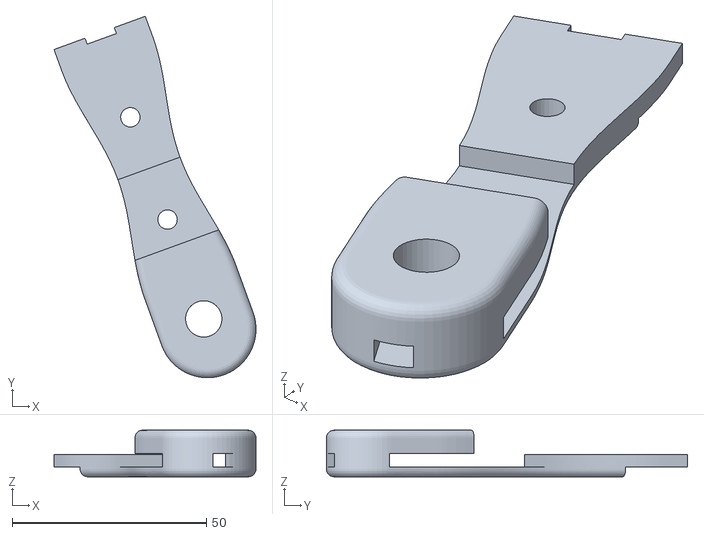
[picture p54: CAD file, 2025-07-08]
3D_files/legs/upper_legBack.stl
52.0 x 93.0 x 12.0

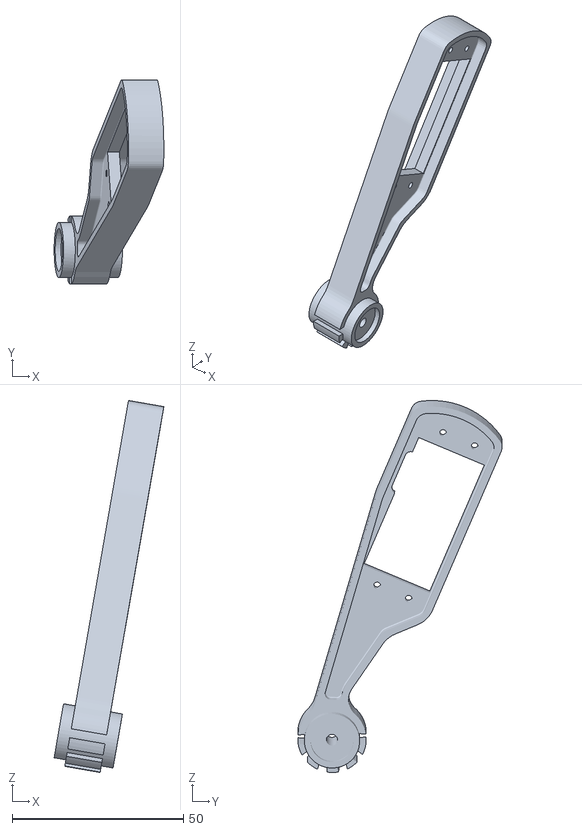
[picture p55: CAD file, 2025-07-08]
3D_files/legs/paw_leg.stl
32.0 x 59.5 x 108.5

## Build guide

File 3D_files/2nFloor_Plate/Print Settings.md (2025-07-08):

| STL FILE | 2nFloor_Plate |
|---|---|
| Material | Sunlu PLA+ |
| Resolution | 0.16mm |
| Infill | 60 % |
| Supports | No |
| Raft | No | 

> [!NOTE]
> Feel free to modify the file as needed to add any holes required for your setup.

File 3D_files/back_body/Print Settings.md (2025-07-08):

| STL FILE |  back_body  |
|---|---|
| Material | Sunlu PLA+  |
| Resolution | 0.16mm |
| Infill | 15% |
| Supports | Yes |
| Raft | No |

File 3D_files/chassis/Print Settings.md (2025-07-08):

| STL FILE | chassis |
|---|---|
| Material | Sunlu PLA+  |
| Resolution | 0.16mm |
| Infill | 80% |
| Supports | Yes |
| Raft | No | 

> [!NOTE]
> Feel free to modify the file as needed to add any holes required for your setup.

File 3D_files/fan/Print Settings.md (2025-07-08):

| STL FILE | fan_blades  | fan_holder  |
|---|---|---|
| Material | Sunlu PLA+  | Sunlu PLA+  |
| Resolution | 0.12mm | 0.16mm |
| Infill | 100% | 20% |
| Supports | No | Yes |
| Raft | No | No |

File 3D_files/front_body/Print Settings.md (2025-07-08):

| STL FILE | front_body  |
|---|---|
| Material | Sunlu PLA+  |
| Resolution | 0.16mm |
| Infill | 50% |
| Supports | Yes |
| Raft | No |

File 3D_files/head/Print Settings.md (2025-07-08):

| STL FILE | head |head_back_panel|
|---|---|---|
| Material | Sunlu PLA+  | Sunlu PLA+ |
| Resolution | 0.16mm | 0.16mm |
| Infill | 15% | 15% |
| Supports | Yes | Yes |
| Raft | No | No |

> [!CAUTION]
> The head file is not a complete head. Simply use the mirror option in your slicer when opening the file and print both halves together, or join them after printing.
>
> (This step is not necessary for the head_back_panel.)

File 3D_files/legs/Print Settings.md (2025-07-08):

*Make sure to print 4 units of each piece
| STL FILE | paw_leg |upper_legBack|upper_legFront|
|---|---|---|---|
| Material | Sunlu PLA+  | Sunlu PLA+  | Sunlu PLA+ |
| Resolution | 0.16mm | 0.16mm | 0.16mm |
| Infill | 80% | 80% | 80% |
| Supports | Yes | Yes | Yes |
| Raft | No | No | No |

> [!TIP]
> To ensure maximum stability, the two upper leg pieces should be permanently bonded using glue or welding after assembly.

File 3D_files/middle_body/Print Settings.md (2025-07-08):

| STL FILE | middle_body |
|---|---|
| Material | Sunlu PLA+  |
| Resolution | 0.16mm |
| Infill | 15% |
| Supports | Yes |
| Raft | No |

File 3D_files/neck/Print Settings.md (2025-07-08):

| STL FILE | Neck |
|---|---|
| Material | PLA |
| Resolution | 0.16mm |
| Infill | 60% |
| Supports | Yes |
| Raft | No |

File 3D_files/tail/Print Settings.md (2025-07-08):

| STL FILE | Tail |
|---|---|
| Material | Sunlu PLA+  |
| Resolution | 0.16mm |
| Infill | 100% |
| Supports | Yes |
| Raft | No | 

> [!NOTE] 
> This component was directly welded to the <a href="https://github.com/joanmarc28/Robocat/blob/main/3D_files/back_body/back_body.stl">back_body</a> to allow their assembly — no glue implied.

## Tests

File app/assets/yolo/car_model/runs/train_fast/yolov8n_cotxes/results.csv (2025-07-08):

epoch | time | train/box_loss | train/cls_loss | train/dfl_loss | metrics/precision(B) | metrics/recall(B) | metrics/mAP50(B) | metrics/mAP50-95(B) | val/box_loss | val/cls_loss | val/dfl_loss | lr/pg0 | lr/pg1 | lr/pg2
1 | 103.78 | 1.13236 | 1.62098 | 1.29627 | 0.78907 | 0.55263 | 0.64763 | 0.44763 | 1.16516 | 1.68229 | 1.22082 | 0.000656863 | 0.000656863 | 0.000656863
2 | 194.135 | 1.1258 | 1.21426 | 1.29006 | 0.70952 | 0.62136 | 0.66814 | 0.44899 | 1.17544 | 1.59635 | 1.3334 | 0.00123618 | 0.00123618 | 0.00123618
3 | 318.611 | 1.10452 | 1.11956 | 1.24413 | 0.60508 | 0.57895 | 0.57973 | 0.32182 | 1.40099 | 1.78746 | 1.48648 | 0.00172749 | 0.00172749 | 0.00172749
4 | 408.577 | 1.07579 | 1.08622 | 1.22588 | 0.80866 | 0.55612 | 0.69317 | 0.43641 | 1.18421 | 1.50411 | 1.29256 | 0.001604 | 0.001604 | 0.001604
5 | 497.288 | 1.0212 | 0.97099 | 1.20482 | 0.87038 | 0.64795 | 0.74931 | 0.50856 | 1.06401 | 1.23986 | 1.25341 | 0.001472 | 0.001472 | 0.001472
6 | 619.48 | 1.19001 | 1.26834 | 1.40081 | 0.84533 | 0.66667 | 0.75965 | 0.47104 | 1.19398 | 1.49843 | 1.38563 | 0.00134 | 0.00134 | 0.00134
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

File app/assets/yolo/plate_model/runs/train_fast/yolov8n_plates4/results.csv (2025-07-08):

epoch | time | train/box_loss | train/cls_loss | train/dfl_loss | metrics/precision(B) | metrics/recall(B) | metrics/mAP50(B) | metrics/mAP50-95(B) | val/box_loss | val/cls_loss | val/dfl_loss | lr/pg0 | lr/pg1 | lr/pg2
1 | 115.661 | 1.56888 | 2.32305 | 1.26292 | 0.63425 | 0.48 | 0.43126 | 0.18772 | 1.87808 | 2.51982 | 1.48487 | 0.00065812 | 0.00065812 | 0.00065812
2 | 269.739 | 1.50172 | 1.5807 | 1.24519 | 0.44484 | 0.46667 | 0.34949 | 0.14088 | 2.08228 | 2.70403 | 1.67245 | 0.00123735 | 0.00123735 | 0.00123735
3 | 447.292 | 1.45905 | 1.36326 | 1.18944 | 0.84488 | 0.50839 | 0.63554 | 0.28554 | 1.94204 | 1.87379 | 1.52293 | 0.00172858 | 0.00172858 | 0.00172858
4 | 579.969 | 1.40168 | 1.20784 | 1.19888 | 0.79064 | 0.69333 | 0.76667 | 0.34904 | 1.90184 | 1.47541 | 1.54888 | 0.001604 | 0.001604 | 0.001604
5 | 691.014 | 1.27241 | 1.09764 | 1.15667 | 0.77614 | 0.68 | 0.73038 | 0.32068 | 1.91848 | 1.34636 | 1.65801 | 0.001472 | 0.001472 | 0.001472
6 | 797.875 | 1.57664 | 1.2442 | 1.3838 | 0.52095 | 0.64 | 0.53448 | 0.22494 | 1.83699 | 1.85298 | 1.40952 | 0.00134 | 0.00134 | 0.00134
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

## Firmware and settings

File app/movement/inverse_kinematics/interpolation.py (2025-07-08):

'''
Per mediar el moviment entre posicions utilitzem inetploacions

Tenim 4 tipus de interpolacions:
    1. Linear (coord)
    2. Parabo (coord)
    3. Square (coord)
    4. Direct (servo)
'''
import movement.inverse_kinematics.position as ik
import numpy as np

def linear_interploation(prev_coord, next_coord, factor):
    (prev_X, prev_Y) = prev_coord
    (next_X, next_Y) = next_coord

    diff_X = next_X - prev_X
    diff_Y = next_Y - prev_Y

    X = prev_X + factor * diff_X
    Y = prev_Y + factor * diff_Y

    coord = (X, Y)
    ik.valid_coord(coord)
    return coord

def parabo_interploation(prev_coord, next_coord, factor, h=0.5):
    (prev_X, prev_Y) = prev_coord
    (next_X, next_Y) = next_coord

    diff_X = next_X - prev_X
    diff_Y = next_Y - prev_Y

    #linear part
    X = prev_X + factor * diff_X
    Y = prev_Y + factor * diff_Y

    #parabolic part
    h_factor = 4 * factor * (1 - factor)
    Y = Y + h*h_factor

    coord = (X, Y)
    ik.valid_coord(coord)

    return coord

def square_interploation(prev_coord, next_coord, factor, h=0.5):
    (prev_X, prev_Y) = prev_coord
    (next_X, next_Y) = next_coord

    diff_X = next_X - prev_X
    diff_Y = next_Y - prev_Y

    linear_distance = np.sqrt(diff_X**2 + diff_Y**2)
    total_distance =  linear_distance + 2*h

    factor_1 = (factor*total_distance)/h
    if factor_1 < 1:
        X = prev_X
        Y = prev_Y + factor_1 * h
    
        coord = (X, Y)
        ik.valid_coord(coord)
        return coord
    
    factor_2 = (factor*linear_distance - h)/linear_distance
    if factor_2 < 1:
        X = prev_X + factor * diff_X
        Y = prev_Y + factor * diff_Y + h
    
        coord = (X, Y)
        ik.valid_coord(coord)
        return coord
    
    factor_3 = (factor*linear_distance - (h+linear_distance))/h
    if factor_3 < 1:
        X = next_X
        Y = next_Y + (1-factor_3) * h
    
        coord = (X, Y)
        ik.valid_coord(coord)
        return coord
    
    return next_coord

def direct_interploation(prev_servo, next_servo, factor):
    (prev_U, prev_D) = prev_servo
    (next_U, next_D) = next_servo

    diff_U = next_U - prev_U
    diff_D = next_D - prev_D

    X = prev_U + factor * diff_U
    Y = prev_D + factor * diff_D

    servo = (X, Y)
    ik.valid_coord(servo)
    return servo

def interpolation(prev_pos, next_pos, factor, method='linear', height=0.5):
    if method=='linear':
        return linear_interploation(prev_pos, next_pos, factor)
    if method=='parabolic':
        return parabo_interploation(prev_pos, next_pos, factor, h=height)
    if method=='square':
        return square_interploation(prev_pos, next_pos, factor, h=height)
    if method=='direct':
        return direct_interploation(prev_pos, next_pos, factor)
    return None

if __name__ == '__main__':
    pass

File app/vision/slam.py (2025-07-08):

import time
import threading

import config
from vision.camera import RobotCamera
from sensors.ultrasonic import ModulUltrasons
from movement.motors import EstructuraPotes
from movement.simulation_data import walk_states

try:
    """from slam.main_slam import SLAMSystem"""

    from external.pyslam.slam import VisualSlam
except Exception as e:  # pragma: no cover - library might not be available
    VisualSlam = None
    print("pyslam not installed: {}".format(e))

class AutonomousSLAM:
    """Basic SLAM driven autonomous movement controller."""

    def __init__(self, camera: RobotCamera | None = None):
        if VisualSlam is None:
            raise RuntimeError(
                "pyslam library is required for AutonomousSLAM to run"
            )

        self.camera = camera or RobotCamera()
        self.ultrasons = ModulUltrasons()
        self.legs = EstructuraPotes(self.ultrasons)
        self.slam = VisualSlam()
        self.running = False

    def process_frame(self):
        frame = self.camera.capture_frame()
        self.slam.track(frame)

    def step_movement(self):
        dist = self.ultrasons.mesura_distancia()
        if dist > config.LLINDAR_ULTRASONIC:
            self.legs.follow_sequance(walk_states, cycles=1, t=0.2)
        else:
            self.legs.follow_order(("move_body", "backward"), t=0.2)

    def run(self):
        self.running = True
        while self.running:
            self.process_frame()
            self.step_movement()
            time.sleep(0.01)

    def stop(self):
        self.running = False


def start_autonomous_slam():
    slam_controller = AutonomousSLAM()
    thread = threading.Thread(target=slam_controller.run, daemon=True)
    thread.start()
    return slam_controller


if __name__ == "__main__":
    controller = start_autonomous_slam()
    try:
        while True:
            time.sleep(1)
    except KeyboardInterrupt:
        controller.stop()

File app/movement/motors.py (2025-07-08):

import math
import time
import config
import board
import busio
import numpy as np
from adafruit_pca9685 import PCA9685
from adafruit_motor import servo
import threading
from sensors.ultrasonic import ModulUltrasons
from movement.simulation_data import *
from movement.inverse_kinematics.steps import position_steps
# Inicialització del bus I2C i la controladora PCA9685
i2c = busio.I2C(board.SCL, board.SDA)
pca = PCA9685(i2c)
pca.frequency = 50  # 50Hz és l’estàndard per a servos

# Inicialitza els 10 primers canals com a servos
servos = []
for i in range(16):
    s = servo.Servo(pca.channels[i], min_pulse=500, max_pulse=2500)
    servos.append(s)


class Pota:
    def __init__(self, cadera, genoll,right,front):
        self.servo_up = cadera
        self.servo_down = genoll
        self.state = "sit"  # Estat inicial de la pota
        self.right = right  
        self.front = front
        self.old_state = "start"

    def set_new_position(self,t, inter_method='linear'):
        new_pos = position(self.state)
        old_pos = position(self.old_state)

        up = 0
        down = 0
        if self.right:
            up = lambda a : 90 - a
            down = lambda a : a
        else:
            up = lambda a : 90 + a
            down = lambda a : 180 - a
        
        correction_factor = (up, down)
        steps = int(t/0.1)

        pos_steps = position_steps(old_pos, new_pos, steps, inter_method, correction_factor)

        up_steps = [pos[0] for pos in pos_steps]
        down_steps = [pos[1] for pos in pos_steps]
        print(up_steps, down_steps)
        t1 = threading.Thread(target=new_angles, args=(self.servo_up,up_steps,t/steps))
        t1.start()
        
        t2 = threading.Thread(target=new_angles, args=(self.servo_down,down_steps,t/steps))
        t2.start()

        t1.join()
        t2.join()


    def up(self):
        #DEPRECATED
        pass

    def down(self, new_state):
        #DEPRECATED
        pass

    def forward(self):  
        self.set_state(forwards(self.state))

    def backward(self):
        self.set_state(backwards(self.state))
    
    def set_state(self, new_state):
        """Estableix un nou estat per a la pota."""
        assert new_state in position_states.keys(), "Invalid state"
        self.old_state = self.state
        self.state = new_state
    

class EstructuraPotes:
    """Classe per gestionar les potes del quadrúpede."""
    def __init__(self,ultrasons: ModulUltrasons=None):
        self.ultrasons:ModulUltrasons = ultrasons

        self.legs = [
            Pota(servos[10], servos[11], True,True),  # Pota 1
            Pota(servos[12], servos[13], False,True),  # Pota 2
            Pota(servos[2], servos[3], True, False),  # Pota 3
            Pota(servos[7], servos[6], False, False)   # Pota 4
        ]
        threads = []

        for leg in self.legs:
            t = threading.Thread(target=leg.set_new_position, args=(0.3,))
            threads.append(t)
            t.start()

        for t in threads:
            t.join()
    
    def set_body_state(self,text):
        for leg in self.legs:
            leg.set_state(text)    

    def set_position(self,text):
        for leg in self.legs:
            leg.set_state(text)
        threads = []
        for leg in self.legs:
            th = threading.Thread(target=leg.set_new_position, args=(0.3,))
            threads.append(th)
            th.start()

        for th in threads:
            th.join()

    def body_forward(self):
        for leg in self.legs:
            leg.backward()

    def body_backward(self):
        for leg in self.legs:
            leg.forward()

    def body_upward(self):
        for leg in self.legs:
            leg.set_state("center")

    def body_downward(self):
        for leg in self.legs:
            leg.set_state("sit")
            
    def sit_hind_legs(self, t=0.2):
        """Sit using only the hind legs while front legs are raised."""
        
        # hind legs
        self.legs[2].set_state("sit_down")
        self.legs[3].set_state("sit_down")
        # raise front legs
        self.legs[0].set_state("up")
        self.legs[1].set_state("up")

        threads = []
        for leg in self.legs:
            th = threading.Thread(target=leg.set_new_position, args=(t,))
            threads.append(th)
            th.start()

        for th in threads:
            th.join()
        
            
    def strech(self, t=0.2):
        """Sit using only the hind legs while front legs are raised."""
        
        # hind legs
        self.legs[2].set_state("up")
        self.legs[3].set_state("up")
        # raise front legs
        self.legs[0].set_state("front_zero")
        self.legs[1].set_state("front_zero")

        threads = []
        for leg in self.legs:
            th = threading.Thread(target=leg.set_new_position, args=(t,))
            threads.append(th)
            th.start()

        for th in threads:
            th.join()
        

    def init_bot(self, t=0.2):
        for leg in self.legs:
            if leg.front:
                leg.set_state("front_zero")
            else:
                leg.set_state("back_zero")
    
        threads = []
        for leg in self.legs:
            th = threading.Thread(target=leg.set_new_position, args=(t,))
            threads.append(th)
            th.start()

        for th in threads:
            th.join()

    #set_positions
    def get_states(self):
        return [leg.state for leg in self.legs]

    """def follow_order(self, order, states, t=1):"""
    def follow_order(self, order,states = None, t=1):
        legs = self.legs
        inter_method = 'linear'

        direction, leg_n, method = order
        
        if method == 'p':
            inter_method = 'parabolic'

        #BODY
        if leg_n == 4:
            if   direction == 'f': 
                self.body_forward()
            elif direction == 'b': 
                self.body_backward()
            elif direction == 'u': 
                self.body_upward()
            elif direction == 'd': 
                self.body_downward()
        
        #LEG
        elif type(leg_n) == int:

            leg = legs[leg_n]
            legs = [leg]

            if direction ==  'f': 
                leg.forward()
            elif direction ==  'b':
                leg.backward()
            elif direction == 'ff':
                leg.forward()
                leg.forward()
        else:
            legs = [legs[i] for i in leg_n]
            for leg in legs:
                leg.set_state(direction)

        new_states = self.get_states()

        #Function move Body
        threads = []
        for leg in legs:
            th = threading.Thread(target=leg.set_new_position, args=(t,inter_method))
            threads.append(th)
            th.start()

        for th in threads:
            th.join()
        return new_states
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
